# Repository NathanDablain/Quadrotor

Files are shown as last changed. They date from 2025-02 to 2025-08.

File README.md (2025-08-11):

Modeling, design, and implementation of an autonomous quadrotor on the AVR64DA48 MCU from Microchip. Consult the Bill of Materials (BOM) within the References folder for a detailed description of components as well as where they can be purchased from. The Ground Controller (GC) was implemented on a Microchip AVR32DA32 MCU, both PCB layouts are contained within the EasyEDA project file within the Electrical folder. The prices included within the BOM for the Flight Controller (FC) and GC PCBs include assembly cost in addition to component and manufacturing cost. Beyond the materials included in the BOM and common hand tools, the following tools are required to make the quadrotor:<br/>
<br/>

| Tool | Recommendation |
|---|---|
| ISP | Atmel ICE |
| Soldering Iron | X-Tronic 3020-XTS |
| 3D Printer | Crealty K1C |
<br/>
<br/>

| Component | Tool Used | Version  |
|---|---|---|
| IDE | Microchip Studio | 7.0.2594 |
| Compiler  | AVR-GCC | 5.4.0 |
| Linker | AVR-GCC | 5.4.0 |
| Assembler | AVR-GCC | 5.4.0 |
<br/>

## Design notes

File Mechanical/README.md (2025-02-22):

This directory will contain all 3D printed parts in both .STL and .SLDPRT file formats as well as the completed assembly.

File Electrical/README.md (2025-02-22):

This directory contains the EasyEDA Project file containing the PCB drawing and layout which can be exported and purchased through a PCB manufacturing company like JLCPCB or PCBway.

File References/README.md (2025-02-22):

This directory contains all relevant datasheets for subcomponents on the Flight Controller (FC) and Ground Controller (GC) PCBs. It also contains a Bill of Materials (BOM) that lists all components.

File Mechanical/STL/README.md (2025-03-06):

These .stl files can be used to 3D print the drone body, arms, and ground controller base.

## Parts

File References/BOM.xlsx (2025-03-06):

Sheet: Overview
Level | Nomenclature | Quantity | Supplier | Unit Cost | Total Cost | Price per g of PLACF: | $0.03
1 | Drone | 1 | self | $187.49 | $187.49
1.1 | Base Assembly | 1 | self | $145.44 | $145.44
1.1.1 | Base | 1 | self | $0.96 | $0.96
1.1.2 | #4-40 Heat Set | 12 | McMaster Carr | $0.17 | $2.05
1.1.3 | Fastener - #4-40 x 1/2 in | 4 | Jameco | $0.15 | $0.60
1.1.4 | 1S (3.7V), 460 mAh LIPO Battery | 1 | GetFPV | $2.50 | $2.50
1.1.5 | 4S (14.8V), 1400 mAh LIPO Battery | 1 | GetFPV | $48.00 | $48.00
1.1.6 | Skystars 4-in-1 3-6S 30x30 ESC | 1 | GetFPV | $42.00 | $42.00
1.1.7 | Flight Controller PCB | 1 | JLCPCB | $51.66 | $51.66
1.2 | Arm Assembly | 2 | self | $21.05 | $42.11
1.1.1 | Arm | 1 | self | $0.33 | $0.33
1.1.2 | Fastener - #4-40 x 1/2 in | 8 | McMaster Carr | $0.17 | $1.36
1.1.3 | VELOX 2306 V3 1500KV BLDC Motor | 1 | GetFPV | $19.00 | $19.00
1.1.4 | 4x4E-3 Propeller | 1 | APC Propellers | $1.55 | $1.55
1.2 | Arm Assembly - short | 2 | self | $21.00 | $42.00
1.1.1 | Arm | 1 | self | $0.27 | $0.27
1.1.2 | Fastener - #4-40 x 1/2 in | 8 | McMaster Carr | $0.17 | $1.36
1.1.3 | VELOX 2306 V3 1500KV BLDC Motor | 1 | GetFPV | $19.00 | $19.00
1.1.4 | 4x4E-3 Propeller | 1 | APC Propellers | $1.55 | $1.55
2 | Ground Controller | 1 | self | $39.67 | $39.67
2.1 | Base Assembly | 1 | self | $0.33 | $0.33
2.1.1 | Base | 1 | self | $1.00 | $1.00
2.1.2 | #4-40 Heat Set | 4 | McMaster Carr | $0.17 | $0.68
2.2 | Ground Controller PCB | 1 | JLCPCB | $36.69 | $36.69
2.3 | Fastener - #4-40 x 1/2 in | 4 | Jameco | $0.15 | $0.60
2.4 | 1S (3.7V), 460 mAh LIPO Battery | 1 | GetFPV | $2.50 | $2.50

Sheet: Flight Controller Expanded
No. | Quantity | Comment | Designator | Footprint | Value | Manufacturer Part | Manufacturer | Supplier Part | Supplier
1 | 1 | 47pF | ANT_C | C0402 | 47pF | 0402CG470J500NT | FH(风华) | C1567 | LCSC
2 | 10 | 100nF | BAR_DC1,BAR_DC2,IMU_DC1,IMU_DC2,LORA_DC1,MAG_DC1,MAG_DC2,MCU_DC1,MCU_DC3,MCU_DC6 | C0402 | 100nF | CL05B104KO5NNNC | SAMSUNG(三星) | C1525 | LCSC
3 | 15 | 1uF | BAR_VR1,BAR_VR2,GPS_VR1,GPS_VR2,IMU_VR1,IMU_VR2,LORA_VR1,LORA_VR2,MAG_VR1,MAG_VR2,MCU_DC2,MCU_DC4,MCU_DC5,MCU_VR1,MCU_VR2 | C0402 | 1uF | CL05A105KA5NQNC | SAMSUNG(三星) | C52923 | LCSC
4 | 6 | XC6206P332MR-G | BAR_VR,GPS_VR,IMU_VR,LORA_VR,MAG_VR,MCU_VR | SOT-23-3_L2.9-W1.6-P1.90-LS2.8-BR |  | XC6206P332MR-G | TOREX(特瑞仕) | C5446 | LCSC
5 | 1 | RST_CAP | C27 | C0603 | 1uF | CL10A105KB8NNNC | SAMSUNG(三星) | C15849 | LCSC
6 | 3 | PZ254V-11-02P | H1,H2,H3 | HDR-TH_2P-P2.54-V-M |  | PZ254V-11-02P | XFCN(兴飞) | C492401 | LCSC
7 | 1 | 2.54-2*3P针 | J1 | HDR-TH_6P-P2.54-V-M-R2-C3-S2.54-1 |  | 2.54-2*3P针 | BOOMELE(博穆精密) | C65114 | LCSC
8 | 1 | U.FL-R-SMT-1(80) | JP1 | RF-SMD_FRF05002-JSS103M |  | U.FL-R-SMT-1(80) | HRS(广濑) | C88374 | LCSC
9 | 1 | 10uF | LORA_DC2 | C0402 | 10uF | CL05A106MQ5NUNC | SAMSUNG(三星) | C15525 | LCSC
10 | 1 | 220nF | MAG_C1 | C0402 | 220nF | CL05B224KO5NNNC | SAMSUNG(三星) | C16772 | LCSC
11 | 1 | 10uF | MAG_DC2a | CAP-SMD_BD6.3-L6.6-W6.6-FD | 10uF | RVT1J100M0605 | ROQANG(容强) | C72489 | LCSC
12 | 1 | 330Ω | RST_RES | R0402 | 330Ω | 0402WGF3300TCE | UNI-ROYAL(厚声) | C25104 | LCSC
13 | 4 | Screw-Hole-M2 | SCREW1,SCREW2,SCREW3,SCREW4 | Screw-Hole-M2
14 | 1 | TS-1187A-B-A-B | SW1 | SW-SMD_4P-L5.1-W5.1-P3.70-LS6.5-TL-2 |  | TS-1187A-B-A-B | XKB Connectivity(中国星坤) | C318884 | LCSC
15 | 1 | lora1276 | U2 | COMM-SMD_LORA1276-C1-915MHZ | lora1276 | lora1276-C1-915MHz | G-NiceRF(思为无线) |  | LCSC
16 | 1 | AVR128DB48-I/PT | U4 | TQFP-48_L7.0-W7.0-P0.50-LS9.0-BL |  | AVR128DB48-I/PT | MICROCHIP(美国微芯) | C1019766 | LCSC
17 | 1 | LPS22HHTR | U6 | HLGA-10L_LPS22HBTR |  | LPS22HHTR | ST(意法半导体) | C2827824 | LCSC
18 | 1 | LSM6DS3TR-C | U7 | LGA-14_L3.0-W2.5-P0.50-TL |  | LSM6DS3TR-C | ST(意法半导体) | C967633 | LCSC
19 | 1 | GPS02-UBX | U8 | WIRELM-SMD_18P-L16.5-W14.5_P1.80-TL |  | GPS02-UBX | G-NiceRF(思为无线) | C5356636 | LCSC
20 | 1 | S8B-PH-K-S(LF)(SN) | U14 | CONN-TH_S8B-PH-K-S-LF-SN |  | S8B-PH-K-S(LF)(SN) | JST | C157915 | LCSC
21 | 1 | FH2.54-09-04PZD | U15 | HDR-TH_4P-P2.54-V-F |  | FH2.54-09-04PZD | XUNPU(讯普) | C7500773 | LCSC
22 | 1 | LIS2MDLTR | U17 | LGA-12_L2.0-W2.0-P0.50-BL |  | LIS2MDLTR | ST(意法半导体) | C919695 | LCSC

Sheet: Ground Controller Expanded
No. | Quantity | Comment | Designator | Footprint | Value | Manufacturer Part | Manufacturer | Supplier Part | Supplier
1 | 4 | 330Ω | B0_RES,B1_RES,B2_RES,RST_RES | R0402 | 330Ω | 0402WGF3300TCE | UNI-ROYAL(厚声) | C25104 | LCSC
2 | 4 | TS-1187A-B-A-B | B0_SW,B1_SW,B2_SW,SW1 | SW-SMD_4P-L5.1-W5.1-P3.70-LS6.5-TL-2 |  | TS-1187A-B-A-B | XKB Connectivity(中国星坤) | C318884 | LCSC
3 | 5 | 100nF | BAR_DC1,BAR_DC2,LORA_DC1,MCU_DC1,MCU_DC3 | C0402 | 100nF | CL05B104KO5NNNC | SAMSUNG(三星) | C1525 | LCSC
4 | 10 | 1uF | BAR_VR1,BAR_VR2,LORA_VR1,LORA_VR2,MCU_DC2,MCU_DC4,MCU_VR1,MCU_VR2,PER_VR1,PER_VR2 | C0402 | 1uF | CL05A105KA5NQNC | SAMSUNG(三星) | C52923 | LCSC
5 | 4 | XC6206P332MR-G | BAR_VR,LORA_VR,MCU_VR,PER_VR | SOT-23-3_L2.9-W1.6-P1.90-LS2.8-BR |  | XC6206P332MR-G | TOREX(特瑞仕) | C5446 | LCSC
6 | 1 | RST_CAP | C27 | C0603 | 1uF | CL10A105KB8NNNC | SAMSUNG(三星) | C15849 | LCSC
7 | 1 | B0_CAP | C28 | C0603 | 1uF | CL10A105KB8NNNC | SAMSUNG(三星) | C15849 | LCSC
8 | 1 | B1_CAP | C29 | C0603 | 1uF | CL10A105KB8NNNC | SAMSUNG(三星) | C15849 | LCSC
9 | 1 | B2_CAP | C30 | C0603 | 1uF | CL10A105KB8NNNC | SAMSUNG(三星) | C15849 | LCSC
10 | 1 | A2541WR-2P | H4 | HDR-TH_2P-P2.54-H-M-W10.0 |  | A2541WR-2P | CJT(长江连接器) | C225488 | LCSC
11 | 1 | 2.54-2*3P针 | J1 | HDR-TH_6P-P2.54-V-M-R2-C3-S2.54-1 |  | 2.54-2*3P针 | BOOMELE(博穆精密) | C65114 | LCSC
12 | 5 | KT-0805G | LED1,LED2,LED3,LED4,LED5 | LED0805-R-RD |  | KT-0805G | KENTO | C2297 | LCSC
13 | 1 | 10uF | LORA_DC2 | C0402 | 10uF | CL05A106MQ5NUNC | SAMSUNG(三星) | C15525 | LCSC
14 | 3 | 500Ω | R1,R2,R3 | RES-ADJ-SMD_RM065-V1 | 500Ω | RM065-501(500R) | BOCHEN(博晨) | C5205017 | LCSC
15 | 5 | 300Ω | R4,R5,R6,R7,R8 | R0805 | 300Ω | 0805W8F3000T5E | UNI-ROYAL(厚声) | C17617 | LCSC
16 | 4 | Screw-Hole-M2 | SCREW1,SCREW2,SCREW3,SCREW4 | Screw-Hole-M2
17 | 1 | lora1276 | U2 | COMM-SMD_LORA1276-C1-915MHZ | lora1276 | lora1276-C1-915MHz | G-NiceRF(思为无线) |  | LCSC
18 | 1 | LPS22HHTR | U6 | HLGA-10L_LPS22HBTR |  | LPS22HHTR | ST(意法半导体) | C2827824 | LCSC
19 | 2 | FH2.54-09-04PZD | U15,U19 | HDR-TH_4P-P2.54-V-F |  | FH2.54-09-04PZD | XUNPU(讯普) | C7500773 | LCSC
20 | 1 | AVR32DA32-I/PT | U18 | TQFP-32_L7.0-W7.0-P0.80-LS9.0-TL |  | AVR32DA32-I/PT | MICROCHIP(美国微芯) | C1016541 | LCSC

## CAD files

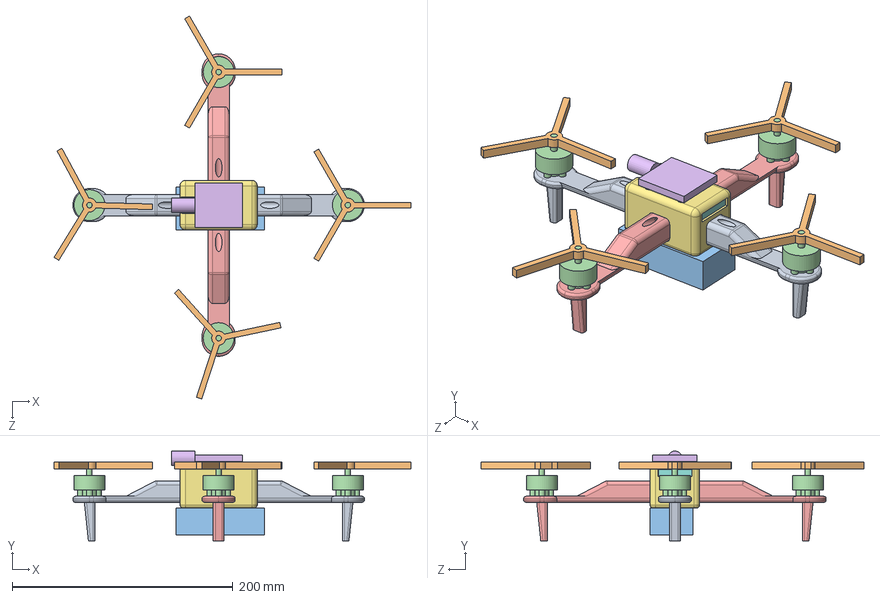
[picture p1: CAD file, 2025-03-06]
Mechanical/Drone_Asm.SLDASM
323.2 x 81.4 x 346.9 mm
1S Battery
Drone_Body_v2
ESC
Drone_Arm x 2
Motor x 4
4S Battery
4x4E-3 x 4
Drone_Arm_Short x 2

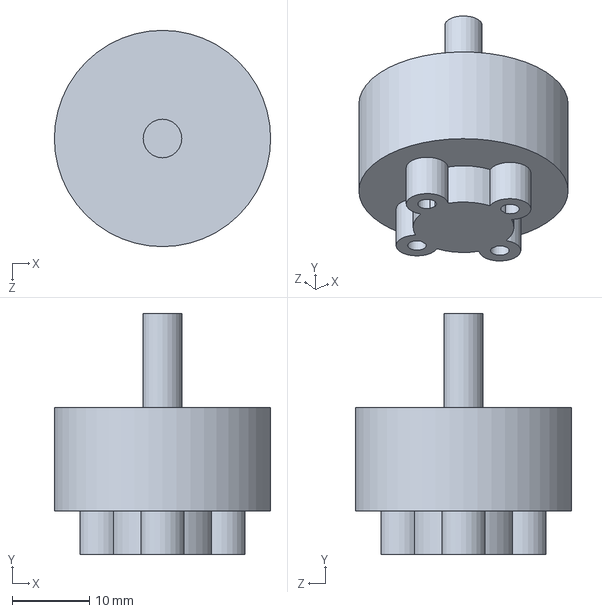
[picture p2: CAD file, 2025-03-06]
Mechanical/Motor.SLDPRT
28.0 x 31.2 x 28.0 mm

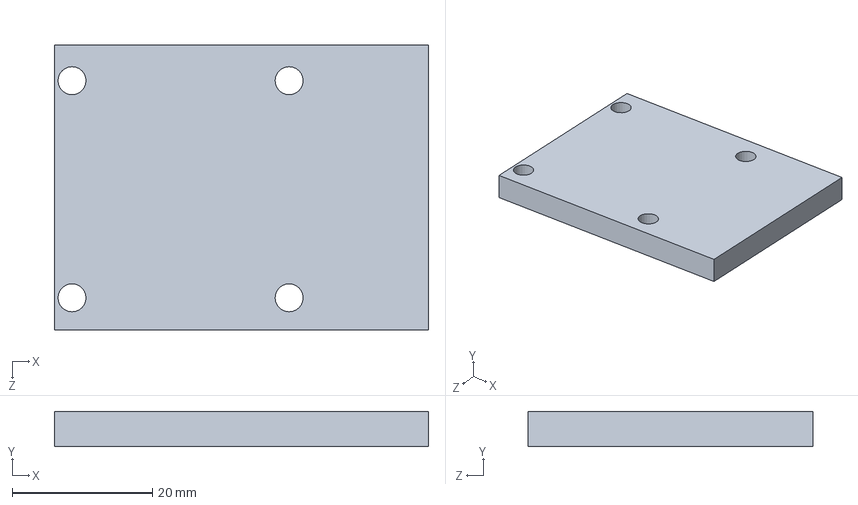
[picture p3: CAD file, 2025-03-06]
Mechanical/MCU.SLDPRT
53.4 x 5.00 x 40.7 mm

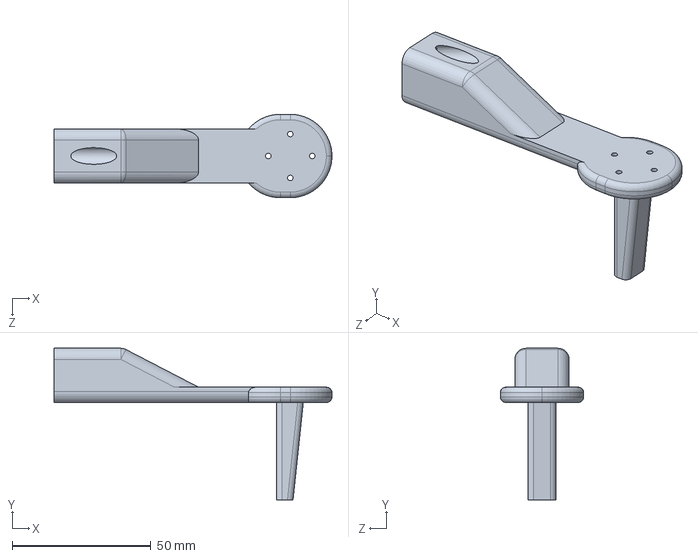
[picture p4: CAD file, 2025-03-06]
Mechanical/Drone_Arm_Short.SLDPRT
100.0 x 54.5 x 30.0 mm

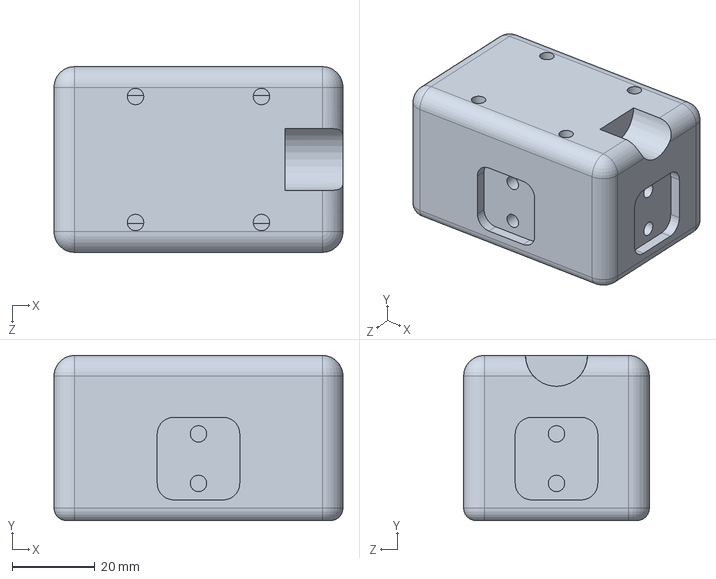
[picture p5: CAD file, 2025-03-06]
Mechanical/Drone_Body_v2.SLDPRT
70.0 x 40.0 x 45.0 mm

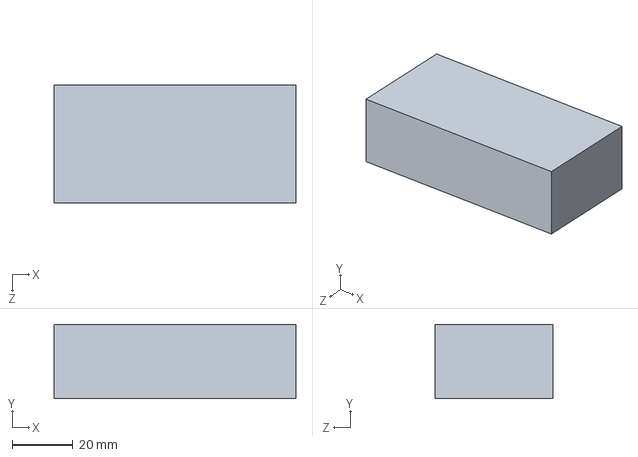
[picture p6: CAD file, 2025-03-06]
Mechanical/4S Battery.SLDPRT
80.0 x 24.5 x 39.0 mm

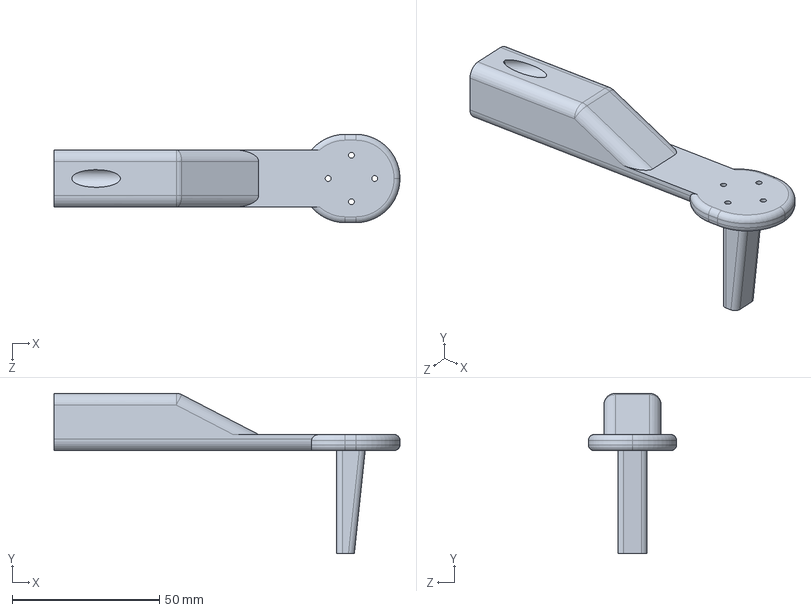
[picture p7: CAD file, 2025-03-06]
Mechanical/Drone_Arm.SLDPRT
117.5 x 54.5 x 30.0 mm

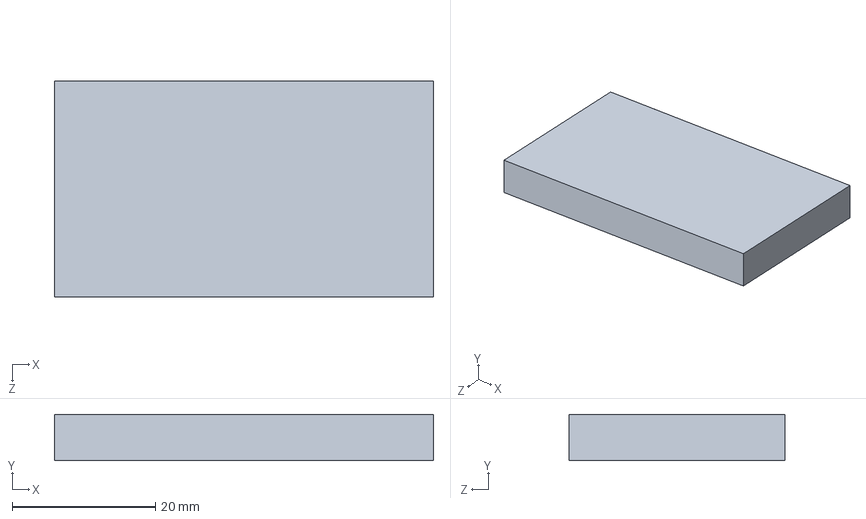
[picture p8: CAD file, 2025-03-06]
Mechanical/1S Battery.SLDPRT
53.0 x 6.50 x 30.2 mm

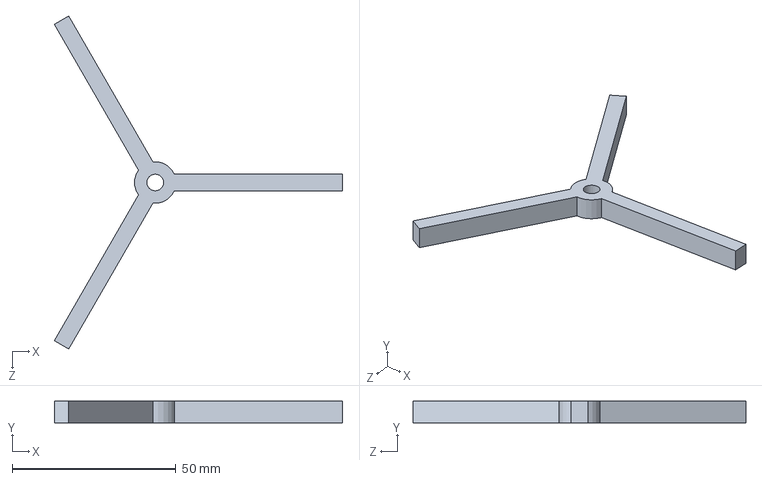
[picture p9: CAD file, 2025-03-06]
Mechanical/4x4E-3.SLDPRT
87.9 x 6.60 x 101.5 mm

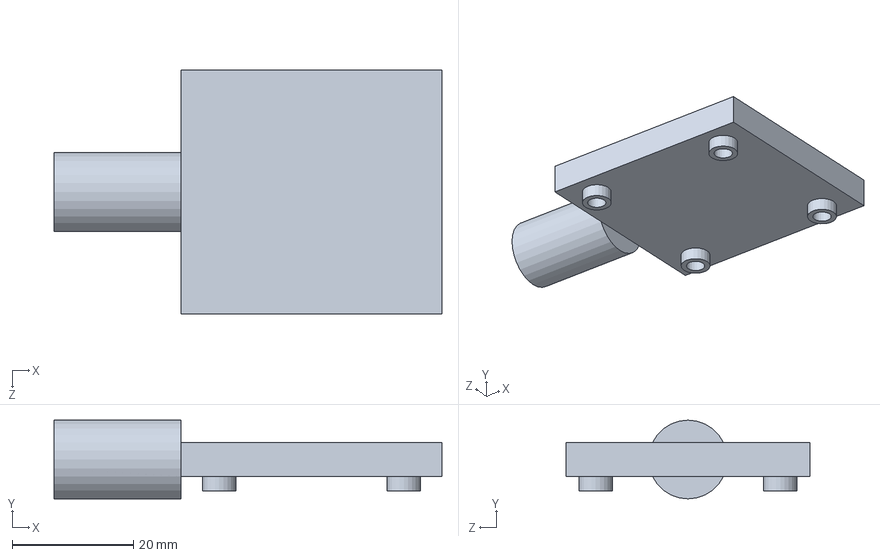
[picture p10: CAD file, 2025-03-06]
Mechanical/ESC.SLDPRT
64.1 x 13.0 x 40.3 mm

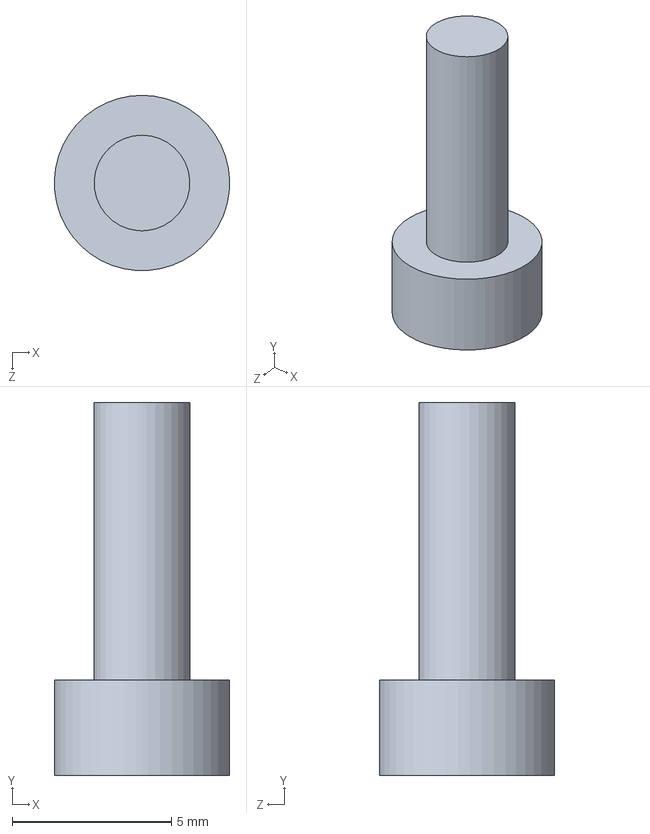
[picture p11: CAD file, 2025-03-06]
Mechanical/Motor_screw.SLDPRT
5.50 x 11.7 x 5.50 mm

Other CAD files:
Mechanical/STL/Drone_Arm.STL
Mechanical/STL/Drone_Arm_Short.STL
Mechanical/STL/Drone_Body_v2.STL

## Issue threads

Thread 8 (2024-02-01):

Delay printing output

NDablain-USAF, 2024-02-01:
Delay printing output while getting bias. Put readouts for "getting fix" or "calibrating"

Closed 2024-02-01.

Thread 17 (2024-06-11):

Motor Test Function

NDablain-USAF, 2024-06-11:
Implement motor test function, try to keep speeds under 600 rad/s. May be issue with initial overshoot on motor start that prevents this.

Closed 2024-07-05.

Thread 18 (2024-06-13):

Add first order height reference point calculation, as a function of time

NDablain-USAF, 2024-06-13:

NDablain-USAF, 2024-06-13:
There will likely be an offset when landing, above or below 0. Add a "close enough" area around the ground to cut out the motors

Closed 2024-07-08.

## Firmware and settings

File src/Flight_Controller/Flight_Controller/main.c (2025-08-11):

#include "Flight_Controller.h"

volatile unsigned long g_seconds = 0;
volatile unsigned char g_print_flag = 0;
volatile unsigned char g_GPS_setup_status = 0;
unsigned char Setup(){
	Setup_Pins();
	if (RSTCTRL_RSTFR & RSTCTRL_PORF_bm){Delay(100000);} // Necessary to stabilize IC's on a cold start
	unsigned char Setup_Bitmask = 0;
	// [7]		[6]		[5]		[4]		[3]		[2]		[1]		[0]
	//					SSD	   LoRa	    MAG		IMU		BAR		GPS
	
	_PROTECTED_WRITE (CLKCTRL_OSCHFCTRLA, (CLKCTRL_FRQSEL_24M_gc|CLKCTRL_AUTOTUNE_bm)); // Sets CPU clock to 24 MHz
	while(!(CLKCTRL_MCLKSTATUS & CLKCTRL_OSCHFS_bm)); // Wait for clock to stabilize
	g_GPS_setup_status = Setup_GPS();
	Setup_SPI();
	Setup_TWI();
	Setup_ADC();
	unsigned char LoRa_setup_status = Setup_LoRa();
	unsigned char MAG_setup_status = Setup_Mag();
	unsigned char IMU_setup_status = Setup_IMU();
	unsigned char BAR_setup_status = Setup_Bar();
	unsigned char SSD_setup_status = Setup_SSD();
	Setup_Bitmask |= (BAR_setup_status<<NAV_BAR_bp) | (IMU_setup_status<<NAV_IMU_bp) | (MAG_setup_status<<NAV_MAG_bp)
	| (LoRa_setup_status<<NAV_LORA_bp) | (SSD_setup_status<<SU_SSD_bp);
	Run_Motors(1);
	Setup_Timers();
	sei();
	return Setup_Bitmask;
}

int main(){
	unsigned char Setup_Bitmask = Setup();
	// If the sensors we need for navigation initialized successfully, enter main loop
	if ((Setup_Bitmask & NAV_SENSORS_bm) == NAV_SENSORS_bm){
		// Initialize data structures
		const Drone_Constants Constants = Initialize_Drone_Constants();
		// Drone-> tracks the current drone states
		States Drone = {0};
		// Desired-> tracks the desired drone states issued by the ground controller
		Reference Desired_States = {0};
		// Commanded-> tracks the states the autopilot is tracking to after the desired states are fed through the guidance functions
		Reference Commanded_States = {0};
		// up_link-> contains the last information sent to the drone via LoRa uplink
		Uplink up_link = {0};
		// Flight_Controller_Status-> Controls the mode of operation the drone is in, changed by uplinks from the ground controller
		FC_Status Flight_Controller_Status = Standby;
		// Holds sensor calibration data 
		Calibration_Data cal_data = {0};
		// Desired_Thrust-> Controlled by state feedback, in units of N
		float Desired_Thrust = 0.0;
		// Desired_Moments-> Controlled by PID, moment order is: body x, body y, body z, in units of N-m
		float Desired_Moments[3] = {0};
		unsigned char reset = 0;
		//unsigned int motor_voltage = 0;
		while(1){
			//--------------Common code--------------//
			// LoRa
			if (g_LoRa_Check_Flag>=2) Run_LORA(&up_link, &Flight_Controller_Status);

			// Printing
			if (g_print_flag &&(Setup_Bitmask & (1<<SU_SSD_bp))){
				g_print_flag = 0;
				char buffer[4][20] = {0};
				unsigned char length_to_print = snprintf(buffer[0], sizeof(buffer[0]), "%4.2f, %4.2f, %4.2f", Drone.Euler[0], Drone.Euler[1], Drone.Euler[2]);
				Print_Page(0, buffer[0], length_to_print);
				length_to_print = snprintf(buffer[1], sizeof(buffer[1]), "%4.2f , %4.2f",-Drone.Position_NED[2],Desired_Thrust);
				Print_Page(1, buffer[1], length_to_print);
				ATOMIC_BLOCK(ATOMIC_FORCEON){
				//length_to_print = snprintf(buffer[2], sizeof(buffer[2]), "%5.5f,%5.5f",Desired_Moments[0], Desired_Moments[1]);
					length_to_print = snprintf(buffer[2], sizeof(buffer[2]), "B %d L %d", g_Motor_Throttles[0],g_Motor_Throttles[1]);
				Print_Page(2, buffer[2], length_to_print);
				//ATOMIC_BLOCK(ATOMIC_FORCEON){
					length_to_print = snprintf(buffer[3], sizeof(buffer[3]), "R %d F %d",g_Motor_Throttles[2],g_Motor_Throttles[3]);
				//}
				Print_Page(3, buffer[3], length_to_print);
				}
			}
			
			// GPS -> Check when full message is received
			if (g_GPS_Read_Flag && g_GPS_setup_status) Read_GPS(&Drone, &cal_data);

			// Barometer -> check 100Hz, samples at 75Hz
			if (g_BAR_Read_Flag >= 2) Read_Bar(&Drone, &cal_data, up_link.Base_altitude);

			// Magnetometer -> check at 200 Hz, samples at 50Hz
			if (g_MAG_Read_Flag) Read_Mag(&Drone, &cal_data);
			
			// Accelerometer -> check at 200 Hz, samples at 52Hz
			if (g_Accel_Read_Flag) Read_Accel(&Drone);

			// Gyro -> Check at 1666Hz, samples at 416Hz
			if (g_Gyro_Read_Flag) Read_Gyro(&Drone, &cal_data); 

			// Attitude Observer update -> 50Hz
			if (g_Attitude_Observer_Update_Flag >= 4) Attitude_Observer_Update(&Drone);
				
			// Attitude Observer predict -> 400Hz
			if (g_Attitude_Observer_Predict_Flag >= 4) Attitude_Observer_Predict(&Drone);

			//--------------Status code-------------//
			if (Flight_Controller_Status == Standby){
				// Initialize or reset calibration data
				if (reset == 0){
					memset(&cal_data, 0, sizeof(cal_data));
					Drone.Latitude = -1;
					Drone.Longitude = -1;
					ATOMIC_BLOCK(ATOMIC_FORCEON){
						memset((unsigned int*)g_Motor_Throttles, 0, sizeof(g_Motor_Throttles));
					}
					reset++;
				}
			}
			else if (Flight_Controller_Status == Calibrating){
				reset = 0;
				
				if (cal_data.bar_cal_status == 0) Calibrate_Bar(&Drone, &cal_data, up_link.Base_altitude);
				
				if (cal_data.mag_cal_status == 0) Calibrate_Mag(&Drone, &cal_data);
				
				if (cal_data.imu_cal_status == 0) Calibrate_IMU(&Drone, &cal_data);
				
				if (Sample_ADC() > MOTOR_VOLTAGE_THRESHOLD){
					cal_data.motor_cal_status = 1;
					g_Motor_Power_Flag = 1;
				}
				//if ((cal_data.motor_cal_status == 0) && (Sample_ADC() > MOTOR_VOLTAGE_THRESHOLD)) Calibrate_Motors(&cal_data);

				if (cal_data.bar_cal_status && cal_data.mag_cal_status && cal_data.imu_cal_status && cal_data.motor_cal_status) Flight_Controller_Status = Ready;
	
			}
			// 200 - b , 280 - l , 250 - r, 200 - f
			else if (Flight_Controller_Status == Ready){
				//static unsigned char motor_checkout_index;
				//static unsigned int motor_checkout_throttle = 10;
				//static unsigned long motor_checkout_timelast;
				//if (g_seconds - motor_checkout_timelast > 1){
					//motor_checkout_throttle -= 1;
					//motor_checkout_timelast = g_seconds;
				//}
				//if (motor_checkout_throttle == 0){
					//motor_checkout_throttle = 10;
					//motor_checkout_index++;
					//if (motor_checkout_index > 3) Flight_Controller_Status = Standby;
				//}
				//g_Motor_Throttles[motor_checkout_index] = motor_checkout_throttle;
			}
			else {
			//------------Guidance and Control functions-------------//
				if (Flight_Controller_Status == Flying){
					if (up_link.Desired_altitude < 5.0){
						Desired_States.Position_NED[2] = -up_link.Desired_altitude;
					}
				}
				else if (Flight_Controller_Status == Landing){
					Desired_States.Position_NED[2] = 1.0;
					if (Drone.Position_NED[2] >= 0){
						Flight_Controller_Status = Standby;
						Desired_Thrust = 0.0;
						memset(Desired_Moments, 0, sizeof(Desired_Moments));
					}
				}
				
				if (g_Guidance_Flag) Run_Guidance(&Desired_States, &Commanded_States);
				
				// Altitude Controller Runs at 100 Hz, updates desired thrust
				if (g_Altitude_Control_Flag >= 2) Desired_Thrust = Altitude_Control(-Drone.Position_NED[2], -Commanded_States.Position_NED[2], &Constants);

				// Euler angle controller and ESCs run at 200 Hz, updates desired motor speeds
				if (g_Motor_Run_Flag){
					g_Motor_Run_Flag = 0;
					Euler_Control(Drone.Euler, Commanded_States.Euler, Desired_Moments, Desired_Thrust, &Constants);
					Set_throttles(Desired_Thrust, Desired_Moments, &Constants);
					Safety_Check(&Drone, &Flight_Controller_Status);
				}
			}
		}

	}
	
	return 0;
}

void Setup_ADC(){
	// Set VDD as ADC voltage reference
	VREF_ADC0REF |= VREF_REFSEL_VDD_gc;
	// Set GND as negative ADC input
	ADC0_MUXNEG |= ADC_MUXNEG_GND_gc;
	// Set oversampling to 64 -> becomes 10 bit ADC
	ADC0_CTRLB |= ADC_SAMPNUM_ACC64_gc;
	// Set extended sampling time
	ADC0_SAMPCTRL = 100;
	// Set MUX position
	ADC0_MUXPOS |= ADC_MUX_ESC;
	// Setup ESC voltage pin to trigger interrupt when brought high for the first time
	ADC_PIN_CTRL |= PORT_ISC_RISING_gc;
	// Enable ADC
	ADC0_CTRLA |= ADC_ENABLE_bm;
}

unsigned int Sample_ADC(){
	// Returns the voltage read in milli volts
	// Begin conversion
	ADC0_COMMAND |= ADC_STCONV_bm;
	// Wait for conversion to finish
	while (!(ADC0_INTFLAGS & ADC_RESRDY_bm));
	unsigned int ADC_result = ADC0_RES;
	ADC_result >>= 6;
	unsigned int voltage_mv = (ADC_result*15) + ADC_result;
	voltage_mv = voltage_mv + (((voltage_mv*7)/10)/5);
	return voltage_mv;
}

void Setup_Timers(){
	//-Setup Real Time Clock for keeping track of total run time-//
	RTC_CTRLA |= RTC_CORREN_bm | RTC_RTCEN_bm;
	RTC_INTCTRL |= RTC_CMP_bm;
	RTC_CMP = 32768;
	//----------------------------------------------------------//
	//--------Setup Timer/Counter A0 for output compare---------//
	// Is triggered every 2.5 ms, is used by:
	//  -> Motors
	TCA0_SINGLE_CTRLA |= TCA_SINGLE_CLKSEL_DIV2_gc;
	TCA0_SINGLE_INTCTRL |= TCA_SINGLE_CMP0_bm | TCA_SINGLE_CMP1_bm | TCA_SINGLE_CMP2_bm;
	//---------------------------------------------------------//
	//-------Setup Timer/Counter B0 for output compare---------//
	// Generates an interrupt every 5 ms, is used by:
	//	-> Magnetometer running at 100 Hz
	//  -> Barometer running at 75 Hz
	//	-> Attitude observer running at 25 Hz
	//	-> Print statements, variable frequency
	//  -> Accelerometer
	TCB0_CTRLA |= TCB_ENABLE_bm | TCB_CLKSEL_DIV2_gc; // Enables timer, uses main clock with a prescaler of two
	TCB0_INTCTRL |= TCB_CAPT_bm; // Enables interrupt on capture
	TCB0_CCMP = 60000; // Value at which timer generates interrupt and resets
	//-------------------------------------------------------//
	//-------Setup Timer/Counter B1 for output compare--------//
	// Generates an interrupt every 0.6002 ms, is used by:
	//	-> Gyro running at 1666 Hz
	//  -> Observer running at 416 Hz
	TCB1_CTRLA |= TCB_ENABLE_bm | TCB_CLKSEL_DIV1_gc;
	TCB1_INTCTRL |= TCB_CAPT_bm;
	TCB1_CCMP = 14405;
#if defined(AVR128DB48)
	//-------------------------------------------------------//
	//-------Setup Timer/Counter B3 for output compare-------//
	// Generates an interrupt every 286 us (3500 Hz), is used by:
	//  -> Oneshot protocol setting motor speed
	TCB2_CTRLA |= TCB_ENABLE_bm | TCB_CLKSEL_DIV1_gc;
	TCB2_INTCTRL |= TCB_CAPT_bm;
	TCB2_CCMP = 5900;
	//----------------------------------------------------------//
	//--------Setup Timer/Counter A1 for output compare---------//
	// Is triggered every 2.5 ms, is used by:
	//  -> Motors
	TCA1_SINGLE_CTRLA |= TCA_SINGLE_CLKSEL_DIV2_gc;
	TCA1_SINGLE_INTCTRL |= TCA_SINGLE_CMP0_bm;
#elif defined(AVR64DA28)
	//-------------------------------------------------------//
	//-------Setup Timer/Counter B2 for output compare-------//
	// Is triggered every 2.5 ms, is used by:
	//  -> Motors
	TCB2_CTRLA |= TCB_CLKSEL_DIV2_gc;
	TCB2_INTCTRL |= TCB_CAPT_bm;
	//----------------------------------------------------------//
	//--------Setup Timer/Counter D for output compare---------//
	// Generates an interrupt every 2.5 ms (400 Hz), is used by:
	//  -> Oneshot protocol setting motor speed
	// In one ramp mode goes CMPASET->CMPACLR->CMPBSET->COMPBCLR
	TCD0_CTRLA |= TCD_CNTPRES_DIV32_gc;
	TCD0_CMPBCLR = 1875;
	TCD0_INTCTRL |= TCD_OVF_bm;
	while(!(TCD0_STATUS & TCD_ENRDY_bm));
	TCD0_CTRLA |= TCD_ENABLE_bm;
#endif
}

ISR(RTC_CNT_vect){
	++g_seconds;
	++g_print_flag;
	RTC_CNT = 0;
	RTC_INTFLAGS = RTC_CMP_bm;
}

ISR(TCB0_INT_vect){
	++g_Motor_Run_Flag;
	++g_Accel_Read_Flag;
	++g_LoRa_Check_Flag;
	++g_BAR_Read_Flag;
	++g_Attitude_Observer_Update_Flag;
	++g_MAG_Read_Flag;
	++g_Altitude_Control_Flag;
	++g_Guidance_Flag;
	TCB0_INTFLAGS = TCB_CAPT_bm;
}

ISR(TCB1_INT_vect){
	++g_Attitude_Observer_Predict_Flag;
	++g_Gyro_Read_Flag;
	TCB1_INTFLAGS = TCB_CAPT_bm;
}

#if defined(AVR128DB48)
ISR(TCB2_INT_vect){
	if (g_Motor_Power_Flag) Run_Motors(0);
	TCB2_INTFLAGS = TCB_CAPT_bm;
}
#elif defined(AVR64DA28)
ISR(TCD0_OVF_vect){
	if (g_Motor_Power_Flag) Run_Motors(0);
	g_Motor_Cal_Flag = 1;
	TCD0_INTFLAGS = TCD_OVF_bm;
}
#endif

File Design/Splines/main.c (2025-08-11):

#include <stdint.h>
#include <stdio.h>
#include <string.h>
#include <stdlib.h>

typedef struct {
    float *data;
    uint8_t length;
} Vector;

typedef struct {
    float Position[3];
    float Velocity[3];
    float Time;
} Line;

void Calculate_Coefficients(Line *Points_to_interpolate, Vector *a_coeff, Vector *b_coeff, Vector *c_coeff, Vector *d_coeff, uint8_t line_index);

void Multiply_row(float *array, float con, uint8_t length);

void Subtract_row(float *left_side, float *right_side, uint8_t length);

int main (void){
    // Allocate memory for interpolation
    Line Points_to_interpolate[3] = {{.Position[0] = 100, .Velocity[0] = -5, .Time = 0.5},
                                     {.Position[0] = 80, .Velocity[0] = -5, .Time = 1.5},
                                     {.Position[0] = 30, .Velocity[0] = -8, .Time = 2.5}};
    uint8_t n = sizeof(Points_to_interpolate)/sizeof(Line);
    // for (uint8_t i = 0; i < n; i++){
    //     Points_to_interpolate[i].Position.data = calloc(3, sizeof(float*));
    //     Points_to_interpolate[i].Position.length = 3;
    //     Points_to_interpolate[i].Velocity.data = calloc(3, sizeof(float*));
    //     Points_to_interpolate[i].Velocity.length = 3;
    //     Points_to_interpolate[i].Time.data = calloc(3, sizeof(float*));
    //     Points_to_interpolate[i].Time.length = 3;
    // }
    Vector a_coeff = {.data = calloc(a_coeff.length, sizeof(*a_coeff.data)), .length = n-1};
    Vector b_coeff = {.data = calloc(b_coeff.length, sizeof(*b_coeff.data)), .length = n};
    Vector c_coeff = {.data = calloc(c_coeff.length, sizeof(*c_coeff.data)), .length = n-1};
    Vector d_coeff = {.data = calloc(d_coeff.length, sizeof(*d_coeff.data)), .length = n-1};
    // Find coefficients for splines between all points
    Calculate_Coefficients(Points_to_interpolate, &a_coeff, &b_coeff, &c_coeff, &d_coeff, 0);

    // Clean up data previously allocated
    free(a_coeff.data);
    free(b_coeff.data);
    free(c_coeff.data);
    free(d_coeff.data);
    // for (uint8_t i = 0; i < n; i++){
    //     free(Points_to_interpolate[i].Position.data);
    //     free(Points_to_interpolate[i].Velocity.data);
    //     free(Points_to_interpolate[i].Time.data);
    // }
    return 0;
}

void Calculate_Coefficients(Line *Points_to_interpolate, Vector *a_coeff, Vector *b_coeff, Vector *c_coeff, Vector *d_coeff, uint8_t line_index){
    // Given velocity at endpoints, solve using clamped method and gaussian elimination
    uint8_t n = b_coeff->length;
    float Matrix[n][n];
    memset(Matrix, 0.0, n*n*sizeof(float));
    float Solns[n];
    memset(Solns, 0.0, n*sizeof(float));
    float h[n-1];
    memset(h, 0.0, (n-1)*sizeof(float));
    float f[n-1];
    memset(f, 0.0, (n-1)*sizeof(float));
    // Solve for dx and dt for each segment we are interpolating between
    for (uint8_t i = 0; i < n-1; i++){
        h[i] = Points_to_interpolate[i+1].Time -  Points_to_interpolate[i].Time;
        f[i] = Points_to_interpolate[i+1].Position[line_index] - Points_to_interpolate[i].Position[line_index];
    }
    // Set up system of linear equations for gaussian elimination
    for (uint8_t i = 0; i < n; i++){
        if (i == 0){
            Matrix[i][0] = (2.0/3.0)*h[0];
            Matrix[i][1] = (1.0/3.0)*h[0];
            Solns[i] = (f[0]/h[0]) - Points_to_interpolate[i].Velocity[line_index];
        }
        else if (i == n-1){
            Matrix[i][n-2] = (1.0/3.0)*h[i-1];
            Matrix[i][n-1] = (2.0/3.0)*h[i-1];
            Solns[i] = Points_to_interpolate[i].Velocity[line_index] - (f[i-1]/h[i-1]);
        }
        else{
            Matrix[i][i-1] = (1.0/3.0)*h[i-1]; // b_i-1
            Matrix[i][i] = (2.0/3.0)*(h[i-1] + h[i]); // b_i
            Matrix[i][i+1] = (1.0/3.0)*h[i]; // b_i+1
            Solns[i] = (f[i]/h[i]) - (f[i-1]/h[i-1]);
        }
    }

    // Use gauss-jordan elimination to solve system of linear equations
    // First work along rows until you get row echelon form, then work backwards to get reduced row echelon form
    // Search along row until you get to the diagonal entry, if any values before this entry are not zero, subtract their value*
    for (uint8_t i = 0; i < n; i++){ // Iterate down rows
        for (uint8_t j = 0; j < i; j++){ // Iterate along row length
            if ((Matrix[i][j] != 0) && (Matrix[j][j] == 1)){
                Solns[i] -= (Solns[j]*Matrix[i][j]);
                float temp[n];
                memcpy(temp, Matrix[j], n*sizeof(float));
                Multiply_row(temp, Matrix[i][j], n);
                Subtract_row(Matrix[i], temp, n);
            }
        }
        if ((Matrix[i][i] != 1)&&(Matrix[i][i] != 0)){
            Solns[i] /= Matrix[i][i];
            Multiply_row(Matrix[i], (1.0/Matrix[i][i]), n);
        }
    }
    // Now work backwards to convert matrix to reduced row echelon form 
    for (uint8_t i = n-1; i>=0; i--){
        for (uint8_t j = n-1; j>i; j--){
            if ((Matrix[i][j] != 0) &&(Matrix[j][j] == 1)){
                Solns[i] -= (Solns[j]*Matrix[i][j]);
                float temp[n];
                memcpy(temp, Matrix[j], n*sizeof(float));
                Multiply_row(temp, Matrix[i][j], n);
                Subtract_row(Matrix[i], temp, n);
            }
        }
    }
}

void Multiply_row(float *array, float con, uint8_t length){
    for (uint8_t i = 0; i<length; i++){
        array[i] *= con;
    }
}

void Subtract_row(float *left_side, float *right_side, uint8_t length){
    for (uint8_t i = 0; i<length; i++){
        left_side[i] -= right_side[i];
    }
}

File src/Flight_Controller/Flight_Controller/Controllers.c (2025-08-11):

#include "Controllers.h"

volatile unsigned char g_Motor_Power_Flag = 0;
volatile unsigned char g_Guidance_Flag = 0;
volatile unsigned char g_Altitude_Control_Flag = 0;
volatile unsigned char g_Motor_Run_Flag = 0;
volatile unsigned char g_Motor_Cal_Flag = 0;
volatile unsigned int g_Motor_Throttles[4] = {0};

Drone_Constants Initialize_Drone_Constants(){
	Drone_Constants Constants = {
	.k_f = 0.000001,
	.k_t = 0.000000011,
	.length_f_b =  0.127,
	.length_l_r = 0.125, 
	.I = {0.0018, 0.00356, 0.00208},
	.mass = 0.5885,
	.KT = 0.006366198,
	.K = 0.006366198/0.000000011,
	.Current = {0.0, 0.1, 0.7, 2.0, 4.1, 7.2, 10.9, 15.4, 20.5, 25.9, 31.8}};
		
	return Constants;
}

void Calibrate_Motors(Calibration_Data *cal_data){
	g_Motor_Power_Flag = 1;
	unsigned int counter = MAX_MOTOR_THROTTLE;
	ATOMIC_BLOCK(ATOMIC_FORCEON){
		g_Motor_Throttles[0] = MAX_MOTOR_THROTTLE;
		g_Motor_Throttles[1] = MAX_MOTOR_THROTTLE;
		g_Motor_Throttles[2] = MAX_MOTOR_THROTTLE;
		g_Motor_Throttles[3] = MAX_MOTOR_THROTTLE;
	}

	Delay(1000000);
	while (counter){
		for (unsigned char i = 0; i < 4; i++){
			ATOMIC_BLOCK(ATOMIC_FORCEON){
				 g_Motor_Throttles[i] = counter;
			}
		}
		while (!g_Motor_Cal_Flag);
		g_Motor_Cal_Flag = 0;
		counter -= 1;
	}
	ATOMIC_BLOCK(ATOMIC_FORCEON){
		 memset((unsigned int*)g_Motor_Throttles, 0, 8);
	}
	cal_data->motor_cal_status = 1;
	Delay(3000000);
}

void Safety_Check(States *Drone, FC_Status *Flight_Controller_Status){
	unsigned char safety_switch = 0;
	
	if (fabs(Drone->Euler[0]) > MOTOR_CUTOFF_ANGLE) safety_switch = 1;
	else if (fabs(Drone->Euler[1]) > MOTOR_CUTOFF_ANGLE) safety_switch = 1;
	else if (fabs(Drone->Position_NED[2]) > MOTOR_CUTOFF_ALTITUDE) safety_switch = 1;
	
	if (safety_switch){
		ATOMIC_BLOCK(ATOMIC_FORCEON){
			memset((unsigned int*)g_Motor_Throttles, 0, 8);
		}
		*Flight_Controller_Status = Standby;
	}
}
	
void Run_Guidance(Reference *Desired_States, Reference *Commanded_States){
	g_Guidance_Flag = 0;
	// IIR to prevent large jumps in reference states
	const float c1 = 0.99;
	const float c2 = 1.0 - c1;
	for (unsigned char i = 0; i < 3; i++){
		Commanded_States->Euler[i] = Commanded_States->Euler[i]*c1 + Desired_States->Euler[i]*c2;
		Commanded_States->Position_NED[i] = Commanded_States->Position_NED[i]*c1 + Desired_States->Position_NED[i]*c2;
	}
}

float Altitude_Control(float h, float h_ref, const Drone_Constants *Constants){
	g_Altitude_Control_Flag = 0;
	// Gains K chosen through pole placement of double integrator
	const float d_t = 0.01;
	const float IIR_c1 = 0.9;
	const float IIR_c2 = 1.0 - IIR_c1;
	const float K[2] = {3.0, 5.0};
	const float K_int = 0.002;
	
	static float e_int;
	static float h_last;
	static float h_dot_last;
	
	e_int += (h_ref-h);
	float h_dot = h_dot_last*IIR_c1 + ((h-h_last)/d_t)*IIR_c2;
	h_dot_last = h_dot;
	h_last = h;
	float u = -K[0]*(h-h_ref) - K[1]*h_dot + K_int*e_int + 9.81;
	float thrust = Constants->mass * u;
	
    return thrust;
}

void Euler_Control(float Current_Euler[3], float Commanded_Euler[3], float desired_moments[3], float thrust, const Drone_Constants *Constants){
    const float d_t = 0.0025;
    const float K[3][2] = {{100.0, 200.0},{100.0, 200.0},{10.0, 20.0}};
	const float K_int = 0.1;
	const float IIR_c1 = 0.9;
	const float IIR_c2 = 1.0 - IIR_c1;
	const float moment_split = 0.75;

	// Because motors cannot run backwards, there is a saturation point for how much moment can be applied that is a function of the thrust
	// Compute the omega (speed^2) expected of each motor to reach this thrust, this becomes maximum control authority for euler control

    static float Euler_last[3];
	static float Euler_dot_last[3];
	static float e_int[3];
	static unsigned char Saturation_Flag[3];
	
	float max_moment_phi = (thrust * Constants->length_l_r)/2.0;
	max_moment_phi *= moment_split;
	float max_moment_theta = (thrust * Constants->length_f_b)/2.0;
	max_moment_theta *= moment_split;
	float max_moment_psi = thrust*(Constants->k_t / Constants->k_f);
	max_moment_psi *= (1.0 - moment_split);
	
    for (unsigned char i = 0; i < 3; i++){
	    float e = Commanded_Euler[i] - Current_Euler[i];
		if ((Saturation_Flag[i] == 0) || ((Saturation_Flag[i] == 1) && (e < 0)) || ((Saturation_Flag[i] == 2) && (e > 0))){
			e_int[i] += e;
		}
	    float Euler_dot = Euler_dot_last[i]*IIR_c1 + ((Current_Euler[i]-Euler_last[i])/d_t)*IIR_c2;
	    Euler_last[i] = Current_Euler[i];
		Euler_dot_last[i] = Euler_dot;
		float u = K[i][0]*e - K[i][1]*Euler_dot + K_int*e_int[i];
	    desired_moments[i] = u * Constants->I[i];
    }
	
	Saturate(&desired_moments[0], max_moment_phi, -max_moment_phi, &Saturation_Flag[0]);
	Saturate(&desired_moments[1], max_moment_theta, -max_moment_theta, &Saturation_Flag[1]);
	Saturate(&desired_moments[2], max_moment_psi, -max_moment_psi, &Saturation_Flag[2]);
}

void Saturate(float *desired_moment, float max, float min, unsigned char* Saturation_Flag){
	if (*desired_moment > max){
		*desired_moment = max;
		*Saturation_Flag = 1;
	}
	else if (*desired_moment < min){
		*desired_moment = min;
		*Saturation_Flag = 2;
	}
	else{
		*Saturation_Flag = 0;
	}
}
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

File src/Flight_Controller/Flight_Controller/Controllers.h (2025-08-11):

#ifndef CONTROLLERS_H
#define CONTROLLERS_H

#include <avr/io.h>
#include <avr/interrupt.h>
#include <util/atomic.h>
#include <math.h>
#include <stdlib.h>
#include <string.h>
#include "LoRa.h"
#include "FC_Types.h"

#define INDEX_NOT_SET 100
#define MOTOR_CUTOFF_ANGLE (45.0*D2R)
#define MOTOR_CUTOFF_ALTITUDE 5.0f
#define MOTOR_VOLTAGE_THRESHOLD 12000 // in milli volts
#define DEADZONE_THROTTLE 275
#define MAX_MOTOR_THROTTLE 1000

typedef struct{
	// Propeller thrust constant N/(rad/s)^2
	float k_f;
	// Propeller torque constant N-m/(rad/s)^2
	float k_t;
	// Distance from front and back motor thrust vectors to drone center of gravity (m)
	float length_f_b;
	// Distance from left and right motor thrust vectors to drone center of gravity (m)
	float length_l_r;
	// Mass moments of inertia
	float I[3];
	// Mass (kg)
	float mass;
	// Motor torque constant in N-m/A (1/KV)
	float KT;
	// Gain to convert (rad/s)^2 to A
	float K;
	// The current produced by the motor for each 10% of throttle, starting at 0%
	float Current[11];
} Drone_Constants;

Drone_Constants Initialize_Drone_Constants();

float Altitude_Control(float h, float h_ref, const Drone_Constants *Constants);

void Euler_Control(float Current_Euler[3], float Commanded_Euler[3], float desired_moments[3], float thrust, const Drone_Constants *Constants);

void Set_throttles(float desired_thrust, float desired_moments[3], const Drone_Constants *Constants);

void Run_Motors(unsigned char setup_flag);

void Run_Guidance(Reference *Desired_States, Reference *Commanded_States);

void Safety_Check(States *Drone, FC_Status *Flight_Controller_Status);

void Calibrate_Motors(Calibration_Data *cal_data);

void Saturate(float *desired_moment, float max, float min, unsigned char* Saturation_Flag);

#endif

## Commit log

2025-03-14 Initial add of motor object, deterministic force and moment model
2025-03-16 Initial add of coordinate frame conversions and environment update
2025-03-19 Initial add of magnetometer model and calibration before normal sim
2025-03-20 Updated sensor axes
2025-03-23 Update to flight controller motor code and sim imu model.
2025-03-25 Initial add of ground controller, updated sim with correct initial states and ground model.
    [Bar.h, Communication.c, LoRa.h]
2025-03-26 Fixed imu reading of linear acceleration
    [Quadrotor.cpp]
2025-03-29 Added adaptive height controller and motor speed mixer
2025-04-02 Fixed quaternion rotation function, added binary search to control motors based off current.
    [Controllers.cpp, Motor.cpp, Motor.h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]
2025-04-03 Improved logging speed, makefile, and yaw control
2025-04-10 Added ground controller functionality, brought more changes from sim into flight controller
2025-04-12 Added common LoRa library, added uplink and downlink support for ground controller
2025-04-13 Added transmit ability for LORA, expanded SSD characters, separate print function
2025-04-22 Split observer into update and prediction functions, increased gyro rate
2025-04-24 Updated all sensors to use FIFOs where possible and achieve desired run rates
2025-05-06 Separated sensor components into separate classes in sim. Changed controller method to pole placement
2025-06-02 Improved handling of FC status, added option to calibrate ESCs
2025-06-08 Sim now accurately models yaw angle in mcu. Updated controllers in sim and FC.
2025-06-30 Fixes ground controller altitude bug, improves controllers
    [Communication.c, Controllers.c, Controllers.cpp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]
2025-07-09 Changes motor throttles to global variable, adds atomic operations on global variables larger than 1 byte, adds conditional compilation for AVR64DA28
